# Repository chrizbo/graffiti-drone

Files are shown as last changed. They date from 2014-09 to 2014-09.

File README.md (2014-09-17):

# Graffiti drone

Tag your favorite (legal) wall with via drone. 

Essentially the Graffiti Drone project is the following:

[GML files](http://www.graffitimarkuplanguage.com/) -> Graffiti Drone -> [Parrot AR Drone 2.0](http://ardrone2.parrot.com/) + Arduino -> Tagged wall

**Warning:** this is still under active development and not everything is completed yet. The flight control is still a bit wonky. Suggestions and feedback are welcome as we finish building and testing...

## Getting started

1. Build your Arduino circuits
2. Print the parts for the drone
3. Setup your Parrot AR Drone 2.0
4. Install the gem
5. Get taggin'

## Arduino

We are using a [Wifi Redback](http://store.linksprite.com/wifi-redback-1-0-arduino-yellowjacket-compatible/) for this setup.

Hardware list:

1. Wifi Redback Yellowjacket compatible Arduino (with USB breakout board to program like the FT232RL)
2. 2 distance sensors (HC-SR04)
3. DC/DC converter (TSR 1-2450) for Redback
4. Custom cable of mini-Tamiya female to split female / raw wires (**mini-Tamiya out of the Parrot AR Drone battery is flipped**)

Solenoid circuit hardware list (with suggestions): 

1. Solenoid (HCNE1-0520) - may be able to find something better for the power/weight tradeoff 
2. Diode (1N4004)
3. Resistor (2.2 kohm)
4. MOSFET transistor (IRLZ44)

The [circuit layout](schematics/graffiti-drone.fzz) can be found in the project under the `schematics` directory.

Steps for Arudino software:

1. Download the [wifi server code](https://github.com/linksprite/ZG2100BasedWiFiShield/zipball/master) and rename as 'CuHead' in your Arduino libraries area
2. Download NewPing library to your Arduino libraries area
3. Update the [`sketches/GraffitiDroneWiServer.ino` sketch](sketches/GraffitiDroneWiServer/GraffitiDroneWiServer.ino) with your wifi hotspot information
4. Compile and upload

Tips and warnings:

* If you don't flip the polarity of the mini-Tamiya coming out of the Parrot AR battery you will blow your diode in the circuit!
* `Arduino Nano w/ ATmega 3281` should be the board selected in the Arduino IDE or you will get an avrdude error when uploading
* Make sure your `CuHead/apps-conf.h` has `APP_WISERVER` uncommented (and the rest commented out)
* Don't attach anything to pins 9-13 of the Redback since that is used for wifi

## Parrot AR Drone

We are using the Parrot AR Drone 2.0 for this project. If you want it to work with a different drone you should replace the `argus` gem with something else and update the GraffitiDrone.rb class to use it.

Update the drone so it will [connect to your wifi network](https://gist.github.com/karlwestin/4051467). You will need to do this every time you unplug the drone since the default settings are restored on startup.

You may want to consider getting a high amperage battery for the drone too to extend flight time and offset the power draw of the Arduino and solenoid.

## 3D printed parts

We use a 3D printer for the various pieces that extend and replace the body of the drone. See the `3d-models` directory for the 3D Rhino and STL files for the additonal parts.

The AR Drone will look like the following with the new parts:

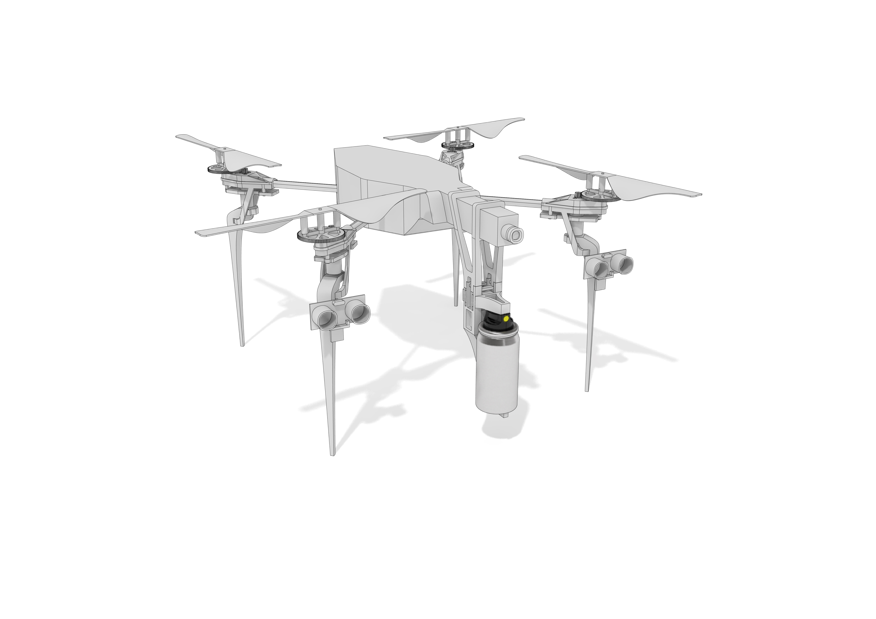
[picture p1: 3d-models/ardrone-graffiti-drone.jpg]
AR Graffiti Drone


## Spray can

We use the [Montana Micro 30 ml spray can](http://www.montanacolors.com/webapp/spray?id=1). You will need to adjust the 3D model if you use something else.

## Software setup

Simple:

`install gem graffiti_drone`

## Running it

Place the drone near a wall (within a foot or two) and run the following command:

`graffiti tag FILE`

`FILE` is the GML file you want the drone to tag.

Console output will keep you up to date on what the drone is trying to do.

## Tests

There are some very limited `rspec` tests that have been added for a few of the modules, but more are needed. 

## Todo

If you want to contribute here are some ideas that we have had that would make the process even better:

* Configurable starting point and size mapping for tags
* Better system for understanding current position on wall (maybe computer vision based?)
* Stencil mode
* Actual PIDs for adjustment of wall distance and yaw

There are also a bunch of places in the code with `TODO` marked for changes and improvements.

## Contributing

1. Fork it ( https://github.com/chrizbo/graffiti_drone/fork )
2. Create your feature branch (`git checkout -b my-new-feature`)
3. Commit your changes (`git commit -am 'Add some feature'`)
4. Push to the branch (`git push origin my-new-feature`)
5. Create a new Pull Request

## License

Code released under the MIT license.

## Contributors

[Chris Butler](http://github.com/chrizbo), [Jason Dembsiky](http://jasondembski.com), [Jon Phillips](http://github.com/rejoin)

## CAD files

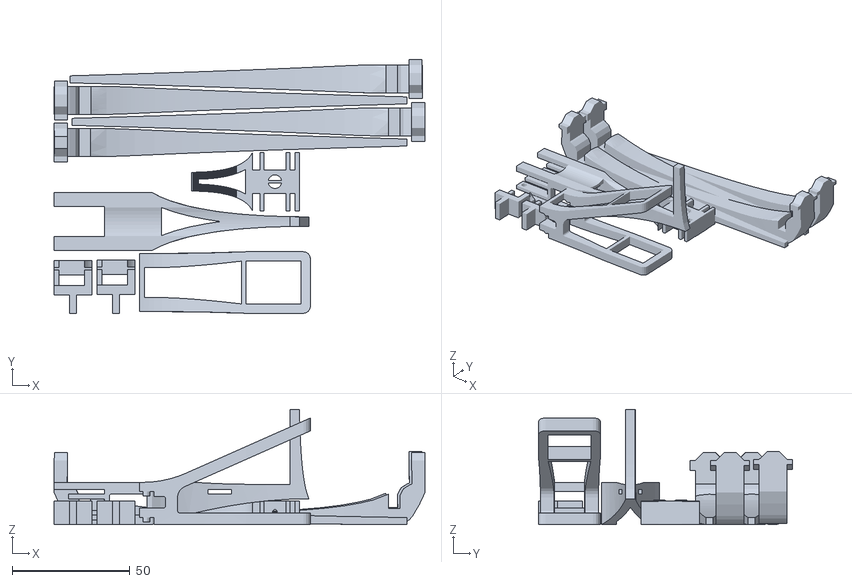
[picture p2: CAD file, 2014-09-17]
3d-models/ardrone-graffiti-drone.stl
157.7 x 108.1 x 49.0

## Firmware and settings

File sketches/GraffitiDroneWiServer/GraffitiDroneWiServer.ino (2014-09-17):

// I stole... I mean borrowed the structure and basics from https://github.com/YuriyGorvitovskiy/ArduinoDccLibrary. Thank you!

#include <WiServer.h>
#include <EEPROM.h>
#include <NewPing.h>

extern "C" {
#include <g2100.h>
}

// Spray can solenoid configuration parameters ------------------------------
#define SPRAY_CAN_SOLENOID_PIN 3

boolean spray_can_activated = false;

// Sonar sensor configuration parameters ------------------------------
#define MAX_DISTANCE    300 // Maximum distance we want to ping for (in centimeters). Maximum sensor distance is rated at 400-500cm.
#define PING_INTERVAL   100

uint8_t current_sensor = 1; // 1 == left and 2 == right

#define LEFT_TRIGGER_PIN  7
#define LEFT_ECHO_PIN     6

unsigned long left_distance = 0;
unsigned long left_ping_timer = 0;
NewPing left_sonar(LEFT_TRIGGER_PIN, LEFT_ECHO_PIN, MAX_DISTANCE); // NewPing setup of pins and maximum distance.

#define RIGHT_TRIGGER_PIN  5
#define RIGHT_ECHO_PIN     4

unsigned long right_distance = 0;
unsigned long right_ping_timer = 0;
NewPing right_sonar(RIGHT_TRIGGER_PIN, RIGHT_ECHO_PIN, MAX_DISTANCE); // NewPing setup of pins and maximum distance.

// Wireless configuration parameters ----------------------------------------
#define SECURITY_TYPE_WEP (1)
#define SECURITY_TYPE_WPA (2)

// WiFi is using pins 9 - LED, 10,11,12,13 (SPI for WiFi communication)
unsigned char local_ip[] = {192,168,1,10};	// IP address of WiShield
unsigned char gateway_ip[] = {192,168,1,253};	// router or gateway IP address
unsigned char subnet_mask[] = {255,255,255,0};	// subnet mask for the local network

const prog_char ssid[] PROGMEM = {"MERCUSYS_C144E4"};	        // max 32 bytes
unsigned char security_type = ZG_SECURITY_TYPE_WEP;

// WPA/WPA2 passphrase
const prog_char security_passphrase[] PROGMEM = {"PASSPHRASE"};	// max 64 characters

// WEP 128-bit keys
// sample HEX keys
prog_uchar wep_keys[] PROGMEM = {	
					0x00, 0x00, 0x00, 0x00, 0x00, 0x00, 0x00, 0x00, 0x00, 0x00, 0x00, 0x00,	0x00,	// Key 0
					0x00, 0x00, 0x00, 0x00, 0x00, 0x00, 0x00, 0x00, 0x00, 0x00, 0x00, 0x00,	0x00,	// Key 1
					0x00, 0x00, 0x00, 0x00, 0x00, 0x00, 0x00, 0x00, 0x00, 0x00, 0x00, 0x00,	0x00,	// Key 2
					0x00, 0x00, 0x00, 0x00, 0x00, 0x00, 0x00, 0x00, 0x00, 0x00, 0x00, 0x00,	0x00	// Key 3
			        };

// setup the wireless mode
// infrastructure - connect to AP
// adhoc - connect to another WiFi device
unsigned char wireless_mode = WIRELESS_MODE_INFRA;

unsigned char ssid_len;
unsigned char security_passphrase_len;

// Wireless configuration parameters ----------------------------------------
void Serial_printMACAddress() {
    Serial.print("MAC Address: ");
    U8* mac = zg_get_mac();
    for (int i = 0; i< 6; ++i) {
        if (i != 0)
            Serial.print(":");
        Serial.print(mac[i], HEX);
    }    
    Serial.println();
}

void Serial_printConnectionState() {
    if(zg_get_conn_state())
        Serial.println("WiFi: Connected");
    else           
        Serial.println("WiFi: Disconnected");
}

// String to char* helper function --------------------------
char* string2char(String command){
    if(command.length()!=0){
        char *p = const_cast<char*>(command.c_str());
        return p;
    }
}

// JSON consstruction helper function ------------------------------------------
String jsonResponse() {
    return String("{ \"leftDistance\": " + String(left_distance) + ", \"rightDistance\": " + String(right_distance) + ", \"spraying\": " + (spray_can_activated ? "true" : "false") + " }");
}

// Main request handling logic -------------------------------
boolean processRequest(char* URL) {
    Serial.print(F("Request: "));
    Serial.println(URL);

    String result = "";
    String sURL(URL);

    if(sURL == "/" || sURL == "/index.json") {
        // if requesting .json then give back the current state of the sensor
        result = jsonResponse();
    } else if(sURL == "/spray/off") {
        // if requesting something like 'spray/off' turn the actuator off
        digitalWrite(SPRAY_CAN_SOLENOID_PIN, LOW);
        spray_can_activated = false;

        result = jsonResponse();
     } else if(sURL == "/spray/on") {
        // if requesting something like '/spray/on' turn the actuator on
        digitalWrite(SPRAY_CAN_SOLENOID_PIN, HIGH);
        spray_can_activated = true;

        result = jsonResponse();
    } else {
        // else give back info about the service and how to use it (aka man page)
        result = "Use /index.json to get the current state.";
    }

    Serial.print(F("Response: "));
    Serial.println(string2char(result));
    WiServer.print(string2char(result));

    return true;
}

// Distance sensor ping ready call back --------------------
void echoCheck() { // If ping received, set the sensor distance to array.
    if(current_sensor == 1 && left_sonar.check_timer()) {
        left_distance = left_sonar.ping_result / US_ROUNDTRIP_CM;
    }

    if(current_sensor == 2 && right_sonar.check_timer()) {
        right_distance = right_sonar.ping_result / US_ROUNDTRIP_CM;
    }
}

// Graffiti Drone WiServer app -----------------------------
void setup() {
    Serial.begin(9600);
    Serial.setTimeout(500); // half a second

    Serial.println(F("Initializing web server..."));
    // Initialize WiServer and have it use the sendMyPage function to serve pages
    WiServer.enableVerboseMode(true);
    WiServer.init(processRequest);    
   
    Serial_printMACAddress();
    Serial_printConnectionState();

    Serial.println(F("Initializing hardware..."));
    pinMode(SPRAY_CAN_SOLENOID_PIN, OUTPUT);
    spray_can_activated = false;

    current_sensor = 1;

    left_ping_timer = millis() + PING_INTERVAL;
    right_ping_timer = left_ping_timer + PING_INTERVAL;

    left_distance = 0;
    right_distance = 0;

    Serial.println(F("Ready"));
}

void loop() {
    // check if it is time to get the results for the left or right sonar
    if(millis() >= left_ping_timer) {               // Is it this sensor's time to ping?
        left_ping_timer += PING_INTERVAL * 2;       // Set next time this sensor will be pinged.
        left_sonar.timer_stop();                    // Make sure previous timer is canceled before starting a new ping (insurance).
        current_sensor = 1;                          // Sensor being accessed.
        left_sonar.ping_timer(echoCheck);           // Do the ping (processing continues, interrupt will call echoCheck to look for echo).
    }

    if(millis() >= right_ping_timer) {              // Is it this sensor's time to ping?
        right_ping_timer += PING_INTERVAL * 2;      // Set next time this sensor will be pinged.
        right_sonar.timer_stop();                   // Make sure previous timer is canceled before starting a new ping (insurance).
        current_sensor = 2;                          // Sensor being accessed.
        right_sonar.ping_timer(echoCheck);          // Do the ping (processing continues, interrupt will call echoCheck to look for echo).
    }

    WiServer.server_task();
    delay(10); // Don't know why but WiServer Works better.
}
